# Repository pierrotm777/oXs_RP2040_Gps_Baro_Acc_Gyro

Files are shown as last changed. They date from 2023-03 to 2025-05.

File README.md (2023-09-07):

# oXs_RP2040_Gps_Baro_Acc_Gyro
 Multi Telemetry Protocols RP2040 Full version
 
## PCBWAY board link
You can find my shared pcb project [here](https://www.pcbway.com/project/shareproject/oXs_RP2040_Full_fdfb35e8.html).

 <object data="http://yoursite.com/the.pdf" type="application/pdf" width="700px" height="700px">
    <embed src="http://yoursite.com/the.pdf">
        <p>This browser does not support PDFs. Please download the PDF to view it: <a href="http://yoursite.com/the.pdf">Download PDF</a>.</p>
    </embed>
</object>

xfun::embed_file("homework.pdf")

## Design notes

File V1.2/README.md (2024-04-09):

# oXs RP2040 Transmitter (version Full telemetry)

This version use my last oXs RP2040 Telemetry board (V1.2).  

## Schematic
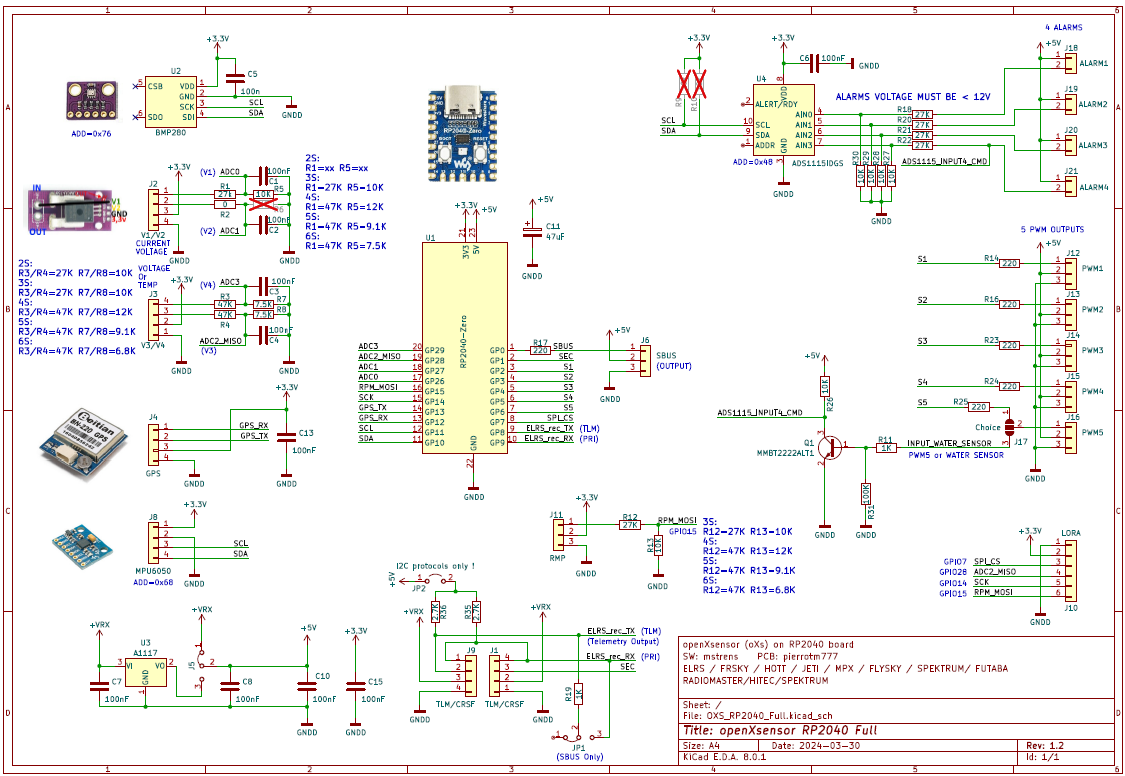
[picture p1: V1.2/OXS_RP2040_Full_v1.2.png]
Schematic
  

## Print Circuit Board
  <table border="2">
  <tr>
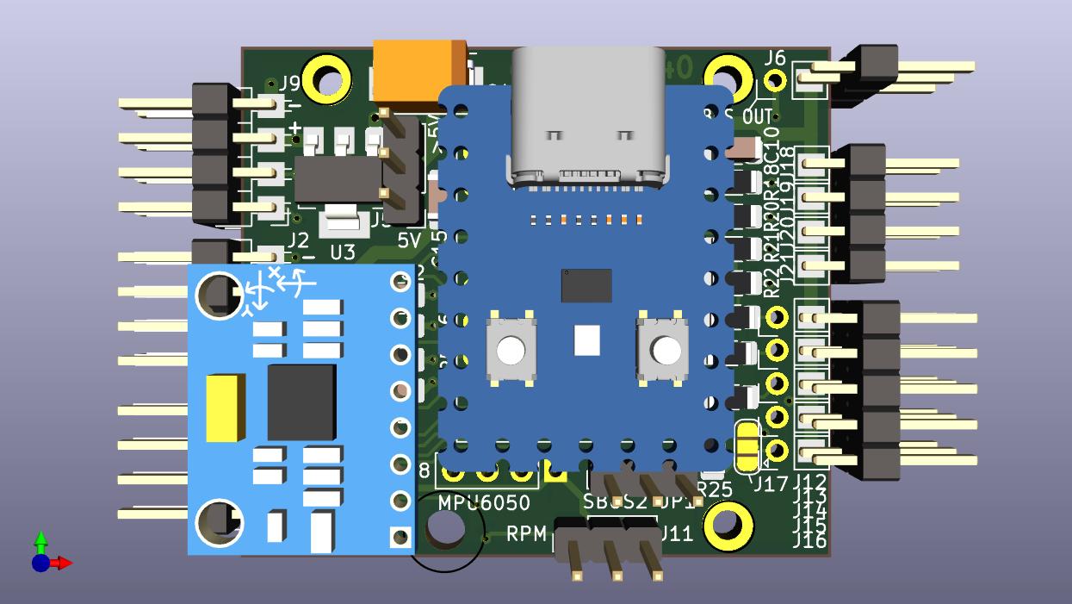
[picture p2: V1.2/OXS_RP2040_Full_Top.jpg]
  <td></td>
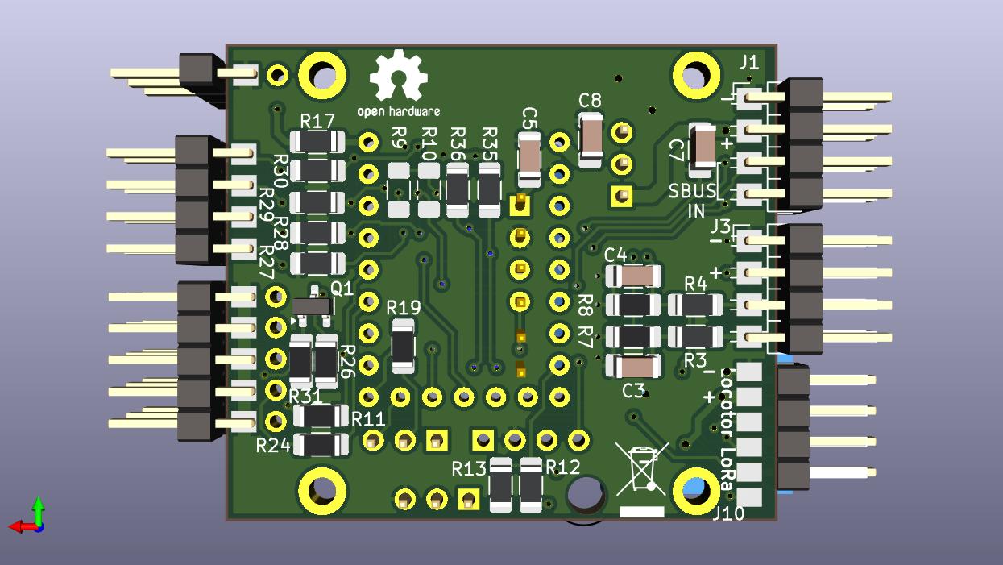
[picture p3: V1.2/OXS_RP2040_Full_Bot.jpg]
  <td></td>
  </tr>
  </table>

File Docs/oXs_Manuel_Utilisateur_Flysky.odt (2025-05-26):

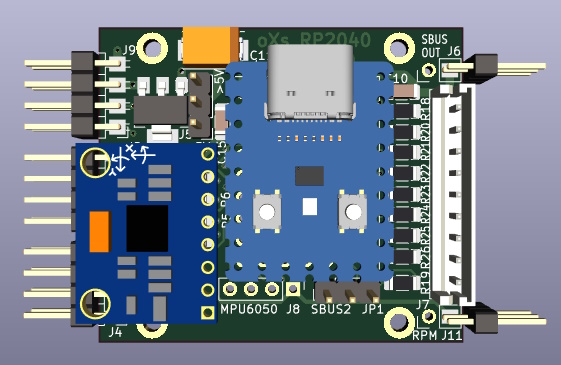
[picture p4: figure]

oXs RP2040

Nouvelle version

openXsensor

pour un RP2040-Zero

Manuel Utilisateur FlySky

# 1 Alimentation

## 1.1 Alimentation du module

Le circuit imprimé est équipé d’un régulateur de tension 5v.

Il peut être mis en ou hors fonction selon l’accu de réception utilisé.

Accus inférieur ou égal à 5V :

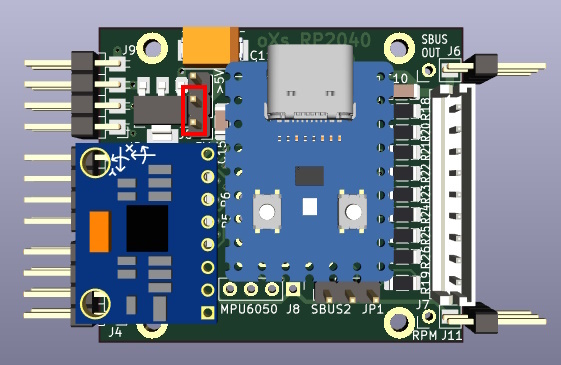
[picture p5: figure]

Accus supérieur à 5V :

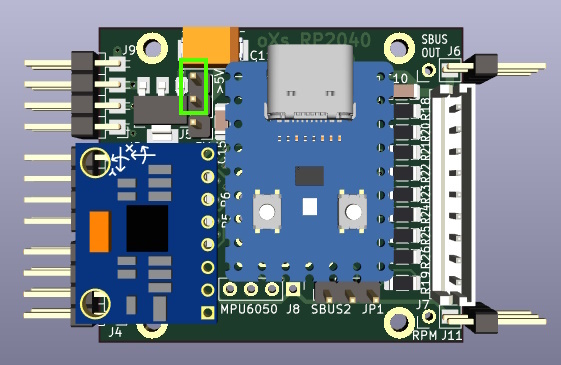
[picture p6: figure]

## 1.2 Limite du RP2040

Le RP2040 ne supporte pas de tension supérieure à 3,3v en entrée !!!!

Toute tension supérieure détruira le composant !!!!

# 2 FlySky IBUS

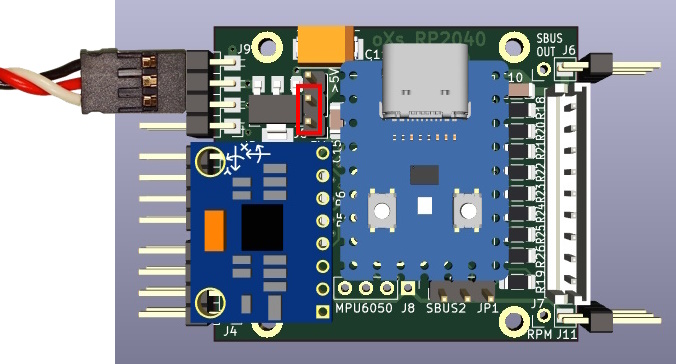
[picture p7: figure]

PROTOCOL=I TLM=8

3 Les capteurs

3.1 Le GPS

Différents récepteurs GPS sont utilisables :

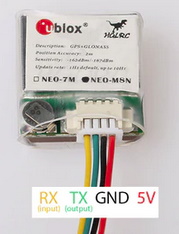
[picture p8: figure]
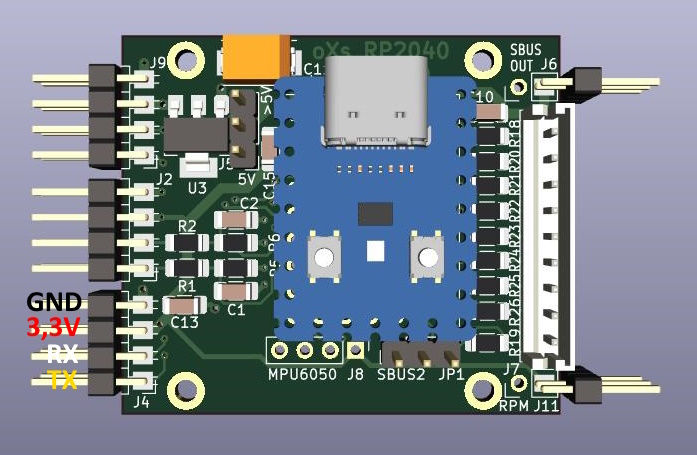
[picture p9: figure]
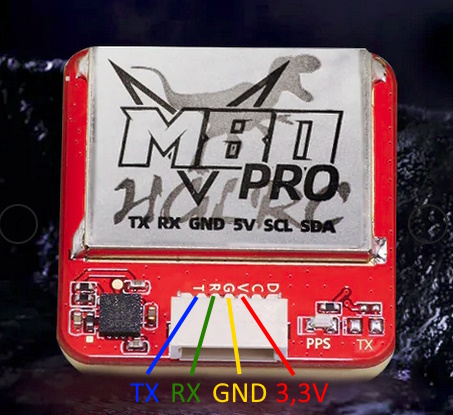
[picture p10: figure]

## 3.2 Le baromètre

Le capteur BMP280 est déjà soudé sous le RP2040.

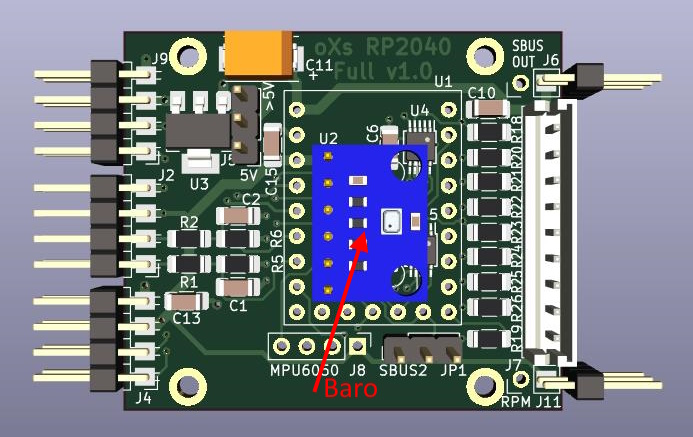
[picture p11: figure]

## 3.3 Sonde Pitot (capteur de pression différentielle)

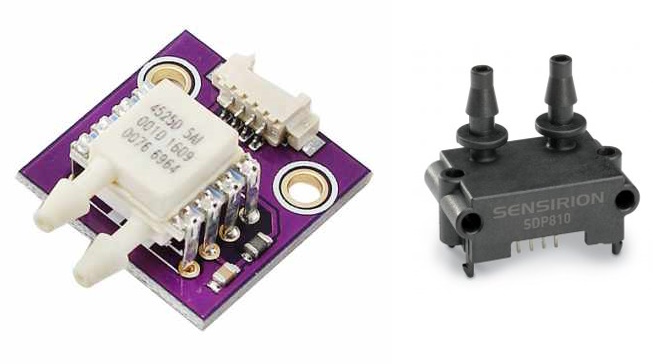
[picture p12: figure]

La sonde Pitot permet de connaître la vitesse horizontale du modèle.

Il permet aussi de calculer la vitesse verticale compensée.

Différents capteurs sont utilisables :

* MS4525D0_A ou SDP3X (x=1,2,3) ou SDP8xx .

Ces capteurs sont chers, les versions SDP sont donc à privilégier.

Ces capteurs sont à câbler sur J8 avec 4 fils, 3,3v, GND, SDA et SCL.

## 3.4 Accéléromètre gyroscope

Ce capteur deux en un permet d’améliorer le temps de réaction du vario ainsi que d’obtenir les données de tangage et roulis.

On peut utiliser un MPU6050 .

Ce capteur est à câbler sur J8 avec 4 fils, 3,3v, GND, SDA et SCL.

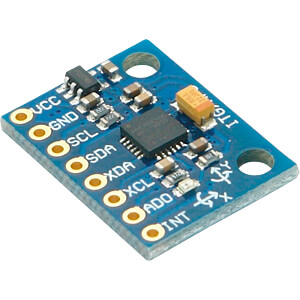
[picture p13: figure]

Après câblage de ce composant, celui-ci doit être calibré.

Pour cela, il doit être placé bien à plat.

Puis on lance la commande suivante :

MPUCAL puis ENTREE

## 3.5 Les entrées analogiques du RP2040

Le RP2040 Zero possède seulement 4 entrées analogiques, V1 à V4.

Elles utilisent les pattes 26 à 29.

V1=26 V2=27 V3=28 V4=29

V1 est attribué au voltage d’un accu de propulsion et V2 au courant consommé.

V3 et V4 retournent deux tensions ou deux températures.

Pour lire des température il faudra définir :

TEMP=1 (V3 retournera une température et V4 une tensions.

Chacune des 4 entrées possèdent un pont de résistance qui doit être calculé en fonction de la tension à lire de sorte que le rp2040 reçoive un maximum de 3,3v pour la tension maximum à lire.

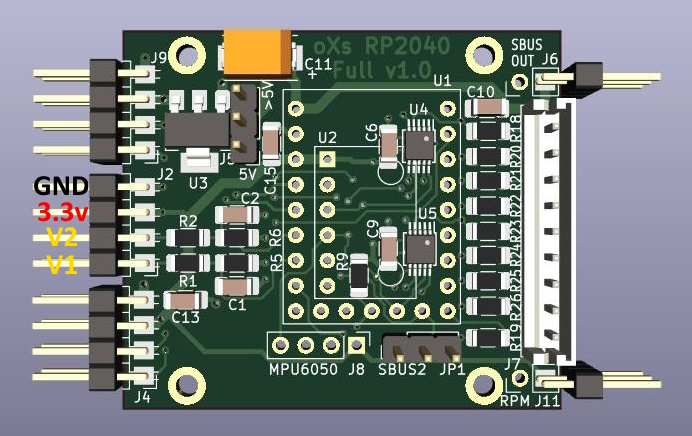
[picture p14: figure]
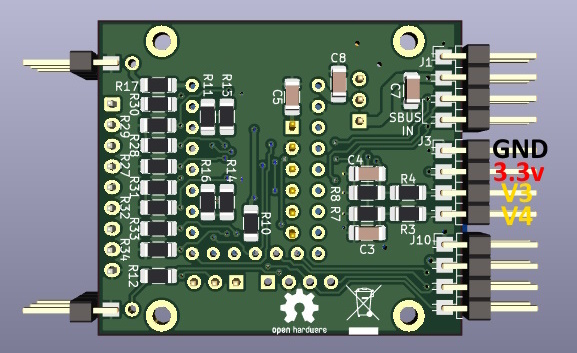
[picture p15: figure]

### 3.5.1 Tension et courant accu moteur (V1/V2)

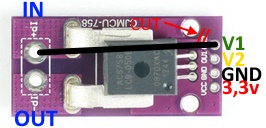
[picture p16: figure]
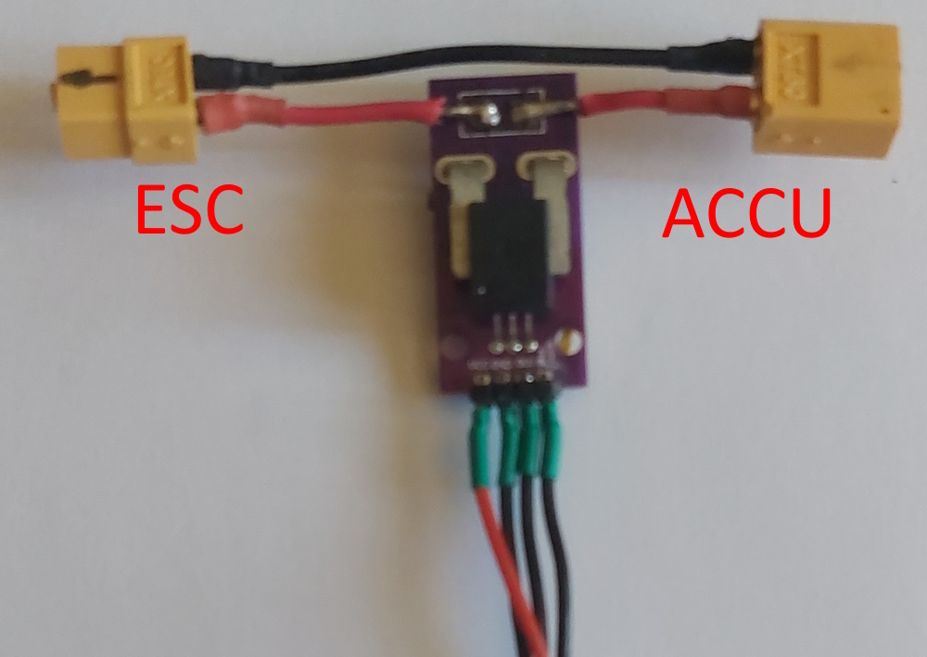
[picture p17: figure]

Pour lire le courant, on utilisera de préférence

un capteur de type ACFS758.

Il en existe différents types avec des courant maximum de 50A à 150A.

La tension de sortie pour les 50B, 100B et 150B est de 1,65 V.

Pas besoin donc de pont de résistance.

### 3.5.2 Tensions V3 et V4

Après câblage des bonnes résistances pour V3 (R4,R8) et V4(R3,R4), il est possible de lire deux tensions supplémentaires.

### 3.5.3 Capteurs de température V3 et V4

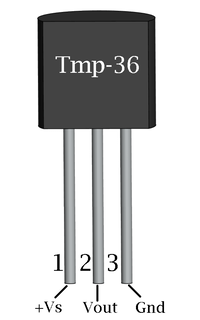
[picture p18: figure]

En fonction du besoin, on peut utiliser un ou deux capteurs de température.

On utilisera de préférence un TMP36.

Pour un seul capteur seulement on définira :

TEMP=1

La sortie de V3 sera utilisée pour ce capteur et V4 sera utilisable pour une tension.

Pour deux capteurs, on définira :

TEMP=2

Les sorties de V3 et V4 seront alors utilisées pour deux températures.

## 3.6 Capteur compte tours

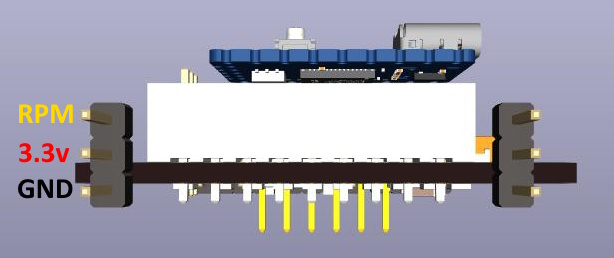
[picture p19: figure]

Ce capteur permet de connaître la vitesse de rotation d’un moteur.

Il utilise la patte 15 du RP2040.

On peut utiliser différents composants ou module.

- capteur Hall

- capteur IR

- module HobbyKing pour ESC

Pour le configurer, on définira :

RPM=15

En fonction du nombre de pales, on attribuera un multiplicateur.

Par exemple pour une hélice à deux pâles :

RPM_MULT=0.5

## 3.7 Les convertisseurs analogiques ADS1115

Les ADS1115, U4 et U5, sont des quadruples convertisseurs analogique/numériques.

Ils permettent de convertir 4 tensions en valeurs numériques.

L’idée d’origine était de palier à la limite de 4 entrées analogiques du RP2040 et de pouvoir

mesurer un accumulateur LIPO 8S maximum (connecteur blanc de droite).

Une autre idée serait d’utiliser ces ADS1115 comme huit entrées d’alarmes.

Il faudrait alors imaginer des alarmes dont le seuil serait définit entre 0 et 3,3v.

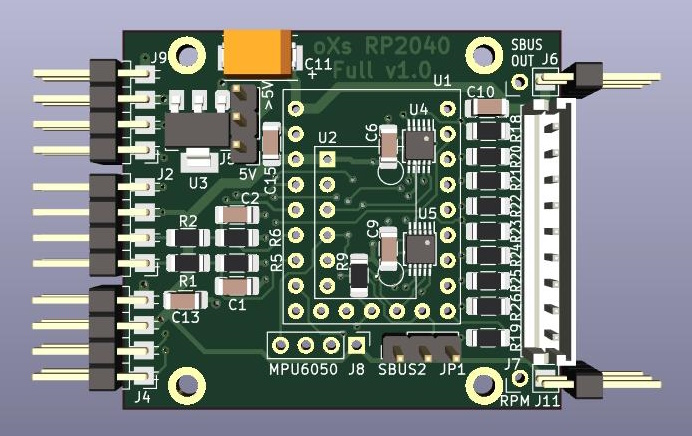
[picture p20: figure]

Pour rappel, le RP2040 ne supporte pas de tension supérieure à 3,3v en entrée !!!!

Toute tension supérieure détruira le composant !!!!

## 3.8 Sorties PWM

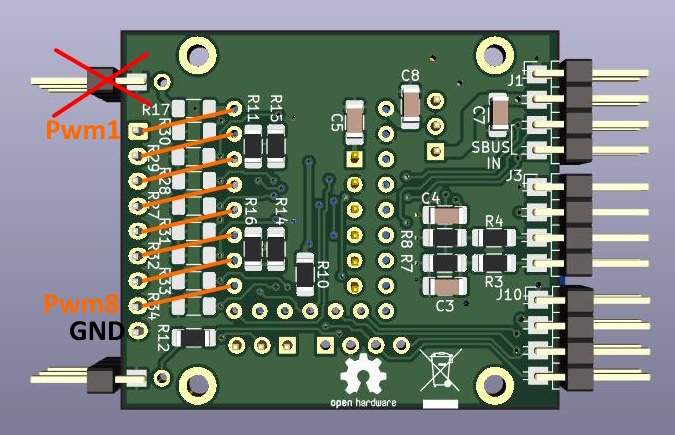
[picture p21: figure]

Si les convertisseurs analogiques ADS1115 ne sont pas utilisés, il est possible d’affecter les pattes 0 à 7 du RP2040 à 8 sorties PWM pour y connecter 8 servos.

Les résistances R18 à R34 placées entre le RP2040 et le connecteur J7 ne doivent pas être câblées.

Il faudra connecter les pattes 0 à 7 du RP2040 aux pattes 1 à 8 de J7.

Voir paragraphe 8 pour la configuration.

# 4 Configuration radio

## 4.1 Recherche des capteurs

- Brancher le module oXs un l’entrée de télémétrie du récepteur Frsky.

- Allumer le récepteur.

- Créer un nouveau modèle avec le protocole Frsky D16 ou D16 EU.

- Réaliser l’appairage du récepteur à l’émetteur (BIND).

- Aller dans l’écran de télémétrie du modèle et lancer une recherche des capteurs.

En fonction des capteurs connectés au module oXs, plusieurs lignes devraient apparaître en plus de la tension accu réception, Rssi etc.

Le GPS ne recevra pas bien s’il est utilisé en intérieur. Il met minimum 1mn pour commencer à recevoir.

Après la découverte d’au moins 4 satellites, les cordonnées ainsi que la date et l’heure, l’altitude, la vitesse horizontale et plus devraient apparaître.

Le baromètre doit retourner l’altitude par rapport au sol ainsi que la vitesse verticale.

Que l’on soit au niveau de la mer ou à 1000m d’altitude, il donnera zéro au démarrage.

C’est donc une altitude relative, pas absolue.

- Stopper la recherche des capteurs.

- Configurer Vario avec Alt .

## 4.1 Utilisation des valeurs de télémétrie dans les écrans

Les radios Frsky ou compatibles qui supportent les firmwares OpenTx ou EdgeTx disposent de pages d’écrans définissables avec ce que l’on souhaite visualiser facilement et rapidement.

On pourra facilement visualiser toutes les valeurs de télémétrie dans ces écrans.

Il est aussi possible de définir des alarmes en fonctions des valeurs de télémétrie reçues.

Page 0 Manuel utilisateur oXs RP2040 v1.0

Page 8 Manuel utilisateur oXs RP2040 v1.0

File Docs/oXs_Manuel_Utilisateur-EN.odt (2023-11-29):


oXs RP2040

New version

openXsensor

for RP2040-Zero

User Manual oXs RP2040

# THIS DOCUMENT

## Versions

Version du Manuel | Date | Raison de l’évolution
1.0 | 12/05/2023 | Création

## Thanks

This project is based on the work of Michel Strens who created the code.

Thanks to him for this wonderful work as well as his listening.

The code can be downloaded from:

https://github.com/mstrens/oXs_on_RP2040.

## Warning

I am in no way responsible for any damage that may result from the misuse or possible malfunction of the oXs RP2040 module, and/or the associated software.

It is therefore up to the end user to measure it, to assume the risks and to respect the legislation in force according to the country of use.

## Content

This document describes the creation of an oXs RP2040 telemetry module as well as its configuration.

## Supported protocols

oXs RP2040 is MULTI protocols.

It supports the following RC telemetry protocols:

ExpressLRS(CRSF)

FRSKY (S-Port or FBUS)

Graupner (HOTT)

Multiplex (M-LINK)

FLYSKY (IBUS)

Futaba ((SBUS2)

Spektrum (SRXL2)

Jeti Ex, Jeti ExBus

This project can be interfaced with 1 or 2 receivers depending on the protocol.

## Fonctions of the oXs RP2040 module

Ce projet est prévu pour générer :

- telemetry data (e.g. when a flight controller is not used)
- PWM and/or
- Sbus signals

For telemetry, it can provide
- up to 4 analog voltages measurement (with scaling and offset) (optional)
- one RPM measurement; a scaling (SCALE4) can be used to take care e.g. of number of blades (optional)
- the altitude and the vertical speed when connected to a pressure sensor (optional)
- the airspeed when connected to a differential pressure sensor (and a pitot tube) (optional)
- compensated vertical speed when connected to a baro + a differentil pressure sensor
- Pitch and Roll when conncted to a MP6050 sensor (optional);
- GPS data (longitude, latitude, speed, altitude,...) (optional)
Note: vertical speed is improved when baro sensor is combined with MP6050 sensor.
t can also provide up to 16 PWM RC channels from a CRSF/ELRS or from 1 or 2 Sbus signal (e.g Frsky or Jeti).

It can also provide SBUS signal (e.g. from 1 or 2 ELRS receivers).
When connected to 2 receivers, the generated PWM and Sbus signals will be issued from the last received Rc channels.
So this provide a kind of redundancy/diversity.

# Présentation d’oXs RP2040

## Vue d’ensemble

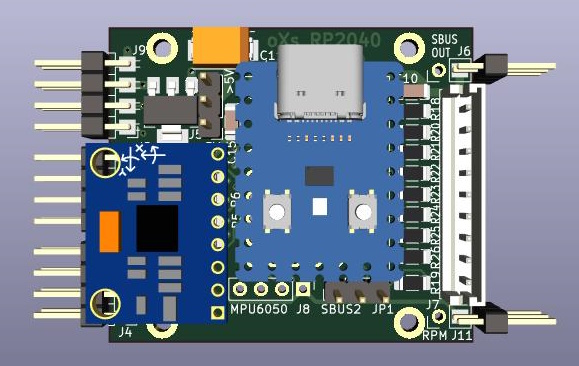
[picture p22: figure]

TX

RX

ELRS / FRSKY (sport + Fbus) / HOTT / JETI Ex/ MPX / FLYSKY / Futaba (SBUS2) / Spektrum (SRXL2)

## Spécifications du module oXs RP2040

Spécification | Valeur / Caractéristique | Note
Alimentation oXs | +5V à +12V | Mettre le cavalier « tension récepteur » sur «5v» ou «>5v» selon la valeur de la tension fournie par le récepteur
Protocoles possibles | ELRS / FRSKY (sport + Fbus) / HOTT / JETI Ex/ MPX / FLYSKY / Futaba (SBUS2) / Spektrum (SRXL2)
Port série USB | | Pour configuration avancée à l’aide d’une application type « Terminal série »
Dimensions | 45mm x 38mm | 4 perçages de 2,2mm

# Schéma du module oXs RP2040 Full

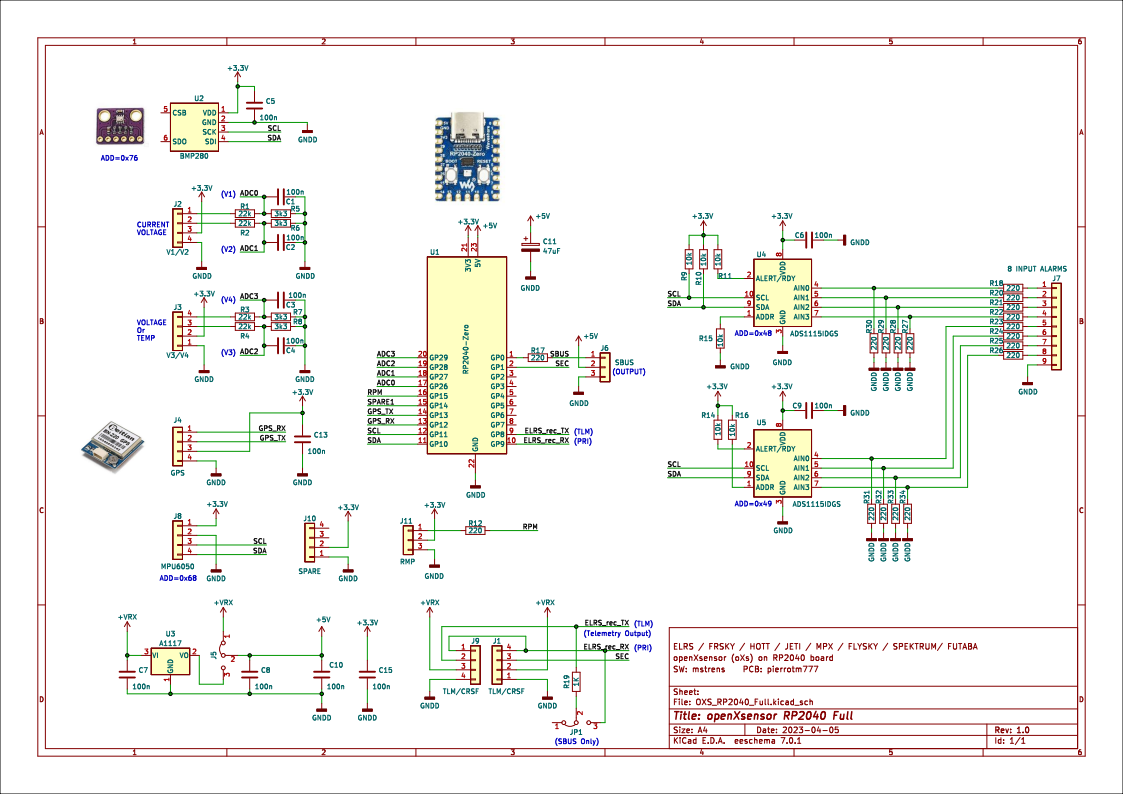
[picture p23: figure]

# Réalisation du module oXs RP2040 Full

## Circuit imprimé

La conception du circuit imprimé du décodeur oXs RP2040 a été réalisée sous KiCad.

Le dossier de fabrication (https://github.com/pierrotm777/oXs_RP2040_Gps_Baro_Acc_Gyro) est disponible sur GitHub.

## 4.2 Carte WaveShare RP2040-Zero

Le module de télémétrie utilise un Rasperri Pico de type RP2040-Zero.

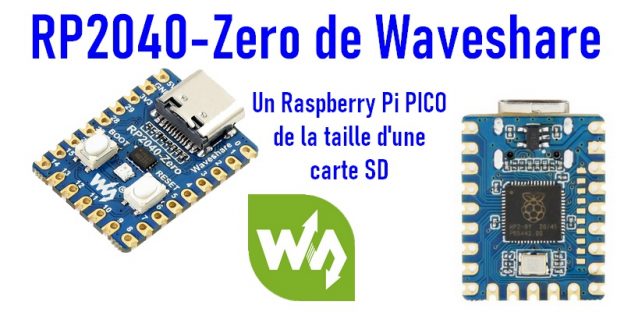
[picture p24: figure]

## 4.3 Téléchargement du Firmware dans le RP2040

Le chargement du Firmware (micro-logiciel embarqué) consiste à copier le contenu d’un fichier uf2 dans la mémoire du micro-contrôleur.

Le fichier oXs.uf2 est à télécharger sur le dépôt GitHub (https://github.com/mstrens/oXs_on_RP2040/tree/test).

## 4.4 Chargement du firmware dans le RP2040

Le RP2040 doit être connecter à votre PC via son connecteur USB tout en maintenant le bouton BOOT.

Une fenêtre doit s’ouvrir. Il suffit de copier le fichier oXs.uf2 pour charger le firmware dans le RP2040.

# 5 Configuration

## 5.1 Connexion au PC

La configuration du module se fait au travers d’un terminal .

Sur Windows, j’utilise Termite (https://www.compuphase.com/software/termite-3.4.exe) de Compuphase ou TeraTerm (https://osdn.net/projects/ttssh2/downloads/74780/teraterm-4.106.exe/) . Other treminals are possible as PuTTY or KiTTY.

A la connexion du RP2040, vous devriez voir apparaître un port COM qui faudra sélectionner.

## 5.2 Configuration du terminal

### 5.2.1 Termite


- Configurez le terminal, puis sélectionnez le port COM (ici le pour COM5).

- La vitesse peut être réglée de 9600 à 115200 sans problème, le code reconnaissant automatiquement la vitesse du terminal.

- Le contrôle de flux doit être définit (DTR/DSR)

### 5.2.2 Tera Term


## 5.3 Configuration

### 5.3.1 Visualiser la configuration du module

Utiliser la touche ENTREE .

Le module doit retourner le résultat suivant :

processing cmd

Cmd to execute:

Version = 2.2.12

Function Pin Change entering XXX=yyy (yyy=255 to disable)

Primary channels input = 255 (PRI = 5, 9, 21, 25)

Secondary channels input = 255 (SEC = 1, 13, 17, 29)

Telemetry . . . . . . . . = 255 (TLM = 0, 1, 2, ..., 29)

GPS Rx . . . . . . . . . = 255 (GPS_RX = 0, 1, 2, ..., 29)

GPS Tx . . . . . . . . . = 255 (GPS_TX = 0, 1, 2, ..., 29)

Sbus OUT . . . . . . . . = 255 (SBUS_OUT= 0, 1, 2, ..., 29)

RPM . . . . . . . . . . = 255 (RPM = 0, 1, 2, ..., 29)

SDA (I2C sensors) . . . . = 255 (SDA = 2, 6, 10, 14, 18, 22, 26)

SCL (I2C sensors) . . . . = 255 (SCL = 3, 7, 11, 15, 19, 23, 27)

PWM Channels 1, 2, 3 ,4 = 255 255 255 255 (C1 / C16= 0, 1, 2, ..., 15)

PWM Channels 5, 6, 7 ,8 = 255 255 255 255

PWM Channels 9,10,11,12 = 255 255 255 255

PWM Channels 13,14,15,16 = 255 255 255 255

Voltage 1, 2, 3, 4 = 255 255 255 255 (V1 / V4 = 26, 27, 28, 29)

Protocol is Sport (Frsky)

CRSF baudrate = 420000

Voltage parameters:

Scales : 1.000000 , 1.000000 , 1.000000 , 1.000000

Offsets: 0.000000 , 0.000000 , 0.000000 , 0.000000

No temperature sensors are connected on V3 and V4

RPM multiplier = 1.000000

Baro sensor is not detected

Acc/Gyro is not detected

Airspeed sensor is not detected

No Vspeed compensation channel defined; oXs uses default settings

First analog to digital sensor is not detected

Second analog to digital sensor is not detected

Foreseen GPS type is Ublox (configured by oXs) :GPS is not (yet) detected

Failsafe type is HOLD

Config parameters are OK

Press ? + Enter to get help about the commands

>>

### 5.3.2 Détails de la configuration

PRI Entrée FBUS SBUS ou EXBUS ou SRXL2

SEC Deuxième Entrée FBUS SBUS ou EXBUS ou SRXL2

TLM Sortie Télémétrie S-PORT JETI M-LINK HOTT

GPS_RX Connexion RX du GPS

GPS_TX Connexion TX du GPS

SBUS_OUT Sortie SBUS (résultat du meilleur signal entre PRI et SEC)

RPM Entrée tachymètre

C1 à C16 Sortie PWM (servos)

V1 à V4 Entrés analogiques (V1 dédié à la tension d’un accus, V2 au courant consommé, V3 et V4 à deux tensions supplémentaires ou deux températures)

Voici la configuration possible fonction du circuit imprimé réalisé :

Version = 2.2.12

Function Pin Change entering XXX=yyy (yyy=255 to disable)

Primary channels input = 9 (PRI = 5, 9, 21, 25)

Secondary channels input = 1 (SEC = 1, 13, 17, 29)

Telemetry . . . . . . . . = 8 (TLM = 0, 1, 2, ..., 29)

GPS Rx . . . . . . . . . = 13 (GPS_RX = 0, 1, 2, ..., 29)

GPS Tx . . . . . . . . . = 12 (GPS_TX = 0, 1, 2, ..., 29)

Sbus OUT . . . . . . . . = 0 (SBUS_OUT= 0, 1, 2, ..., 29)

RPM . . . . . . . . . . = 15 (RPM = 0, 1, 2, ..., 29)

SDA (I2C sensors) . . . . = 10 (SDA = 2, 6, 10, 14, 18, 22, 26)

SCL (I2C sensors) . . . . = 11 (SCL = 3, 7, 11, 15, 19, 23, 27)

PWM Channels 1, 2, 3 ,4 = 2 3 4 5 (C1 / C16= 0, 1, 2, ..., 15)

PWM Channels 5, 6, 7 ,8 = 255 255 255 255

PWM Channels 9,10,11,12 = 255 255 255 255

PWM Channels 13,14,15,16 = 255 255 255 255

Voltage 1, 2, 3, 4 = 255 255 255 255 (V1 / V4 = 26, 27, 28, 29)

Dans ce premier tableau, on affecte une fonction à une patte du RP2040.

L’affectation des pattes ne doit bien sûr pas être modifiée car il y aurait incompatibilité avec le circuit imprimé.

Les pattes ayant la valeur 255 ne sont pas définies.

PRI sera toujours égal à la patte 9 (mais il peut être aussi égal à 5, 9, 21 ou 25).

SEC sera toujours égal à la patte 1 ( mais il peut aussi être égal à 1, 13, 17 ou 29).

etc...

Mais, en fonction du protocole choisi et des fonctions utilisées, certaines pattes resteront à 255 donc non définies.

Pour définir une patte, il suffit de taper dans le terminal TLM=8 par exemple ou TLM=255 pour la désaffecter.

Pour connaître toutes les commandes disponibles, il suffit de taper ? puis ENTREE.

Commands can be entered to change the config parameters

- To activate a function, select the pin and enter function code = pin number (e.g. PRI=1)

Function Code Valid pins number

Primary channels input PRI = 5, 9, 21, 25

Secondary channels input SEC = 1, 13, 17, 29

Telemetry TLM = 0, 1, 2, ..., 29

GPS Rx GPS_RX = 0, 1, 2, ..., 29

GPS Tx GPS_TX = 0, 1, 2, ..., 29

Sbus OUT SBUS_OUT= 0, 1, 2, ..., 29

RPM (only for Sport) RPM = 0, 1, 2, ..., 29

SDA (baro sensor) SDA = 2, 6, 10, 14, 18, 22, 26

SCL (baro sensor) SCL = 3, 7, 11, 15, 19, 23, 27

PWM Channels 1, ..., 16 C1 / C16= 0, 1, 2, ..., 15

Voltage 1, ..., 4 V1 / V4 = 26, 27, 28, 29

- To disable a function, set pin number to 255

-To debug on USB/serial the telemetry frames, enter DEBUGTLM=Y or DEBUGTLM=N (default)

-To change the protocol, enter PROTOCOL=x where x= S(Sport Frsky), F(Fbus Frsky), C(CRSF/ELRS), H(Hott), M(Mpx), 2(Sbus2 Futaba), J(Jeti), E(jeti Exbus), X (spektrum SRXL2) ,or I(IBus/Flysky)

-To change the CRSF baudrate, enter e.g. BAUD=420000

-To change voltage scales, enter SCALEx=nnn.ddd e.g. SCALE1=2.3 or SCALE3=0.123

Enter SCALEx=0 to avoid sending voltage x to the Transmitter (for Frsky or Jeti)

-If a TMP36 is used on V3, enter TEMP=1 (if a second one is on V4, enter TEMP=2)-To change voltage offset, enter OFFSETx=nnn.ddd e.g. OFFSET1=0.6789

-To change GPS type: for an Ublox, enter GPS=U (configured by oXs) or E (configured Externally) and for a CADIS, enter GPS=C

-To change RPM multiplicator, enter e.g. RPM_MULT=0.5 to divide RPM by 2

-To force a calibration of MP6050, enter MPUCAL

-To use a channel to setup Airspeed compensation factor and/or to select between the 2 Vspeed, enter the channel with ACC=1...16-To select the failsafe mode to HOLD, enter FAILSAFE=H

-To set the failsafe values on the current position, enter SETFAILSAFE

-To get the internal telemetry values currently calculated by oXs, enter FV (meaning Field Values)

-To test a protocol, you can force the internal telemetry values to some dummy values for dummy positive values, enter FVP; for dummy negative values, enter FVN

-To get the current PWM values (in micro sec, enter PWM)-To get the current config, just press Enter

Note: some changes require a reset to be applied (e.g. to unlock I2C bus)

En cas d’erreur de configuration le module en fait la remarque, par example :

Error in parameters: a pin is defined for Sbus Out but not for Primary nor Secondary channels input (PRI or SEC)

Attention: error in config parameters

### 5.3.3 Définition du protocole de télémétrie

Selon le protocole, les broches utilisées pour les canaux RC PRIMAIRES/SECONDAIRES et pour la télémétrie (TLM) varient

Protocole | PRI | SEC | TLM | Commentaire
C(ELRS) | (TX de Rx1) | (TX de Rx2) | (RX de RX1)
S(Frsky sport) | (Sbus de Rx1) | (Sbus de Rx2) | (Sport de RX1 ou Rx2) | (1)
F(Frsky Fbus) | Fbus de Rx1 | (Sbus de Rx2) | Non utilisé | (2)
J(Jeti ex) | (Sbus de Rx1) | (Sbus de Rx2) | (Ex de Rx1 ou Rx2)
E(Jeti Exbus) | Exbus de Rx1 | (Sbus de Rx2) | Non utilisé | (2)
H(Hott) | (Sbus de Rx1) | (Sbus de Rx2) | (tlm de RX1 ou Rx2) | (1)
M(Multiplex) | (Sbus de Rx1) | (Sbus de Rx2) | (tlm de RX1 ou Rx2) | (1)
I(Flysky Ibus) | (Sbus de Rx1) | (Sbus de Rx2) | (Ibus de RX1 ou Rx2) | (1)
L(Spektrum Srxl2) | Srxl de Rx1 | Non utilisé | Non utilisé | (2)
2(Futaba Sbus2) | Sbus2 de Rx1 | (Sbus de Rx2) | Sbus2 de Rx1 via 1Kohm | (3)

# Remarque : les broches entre () signifient qu'elles sont facultatives.

(1) pour la sécurité, insérez une résistance de 1 kOhm entre la broche TLM et Rx

(2) pour la sécurité, insérez une résistance de 1 kOhm entre la broche PRI et Rx

(3) Pour Futaba, la broche TLM doit être égale à la broche PRI - 1 et insérer une résistance de 1 kOhm entre PRI et TLM

Pour plus de détails, lire le fichier Readme.md (https://github.com/mstrens/oXs_on_RP2040/blob/main/README.md) .

# 6 Câblage

## 6.1 Alimentation du module

Le circuit imprimé est équipé d’un régulateur de tension 5v.

Il peut être mis en ou hors fonction selon l’accu de réception utilisé.

Accus inférieur ou égal à 5V :


Accus supérieur à 5V :


## 6.2 Limite du RP2040

Le RP2040 ne supporte pas de tension supérieure à 3,3v en entrée !!!!

Toute tension supérieure détruira le composant !!!!

# 7 Les protocoles

## 7.1 S-Port, Hott, M-Link, Ibus, Jeti Ex


S-Port PROTOCOL=S

Hott PROTOCOL=H

M-link PROTOCOL=M

Ibus PROTOCOL=I

Jeti Ex PROTOCOL=J

PRI=255 SEC=255 TLM=8

## 7.2 Sbus2, Srxl2, Jeti ExBus, Fbus


Sbus2 PROTOCOL=2

Fbus PROTOCOL=F

Srxl2 PROTOCOL=L

Jeti Exbus PROTOCOL=E

PRI=9 SEC=255 TLM=255

## 7.2 ExpressLRS (CRSF)


PROTOCOL C PRI=9 TLM=8 SBUS_OUT=0

ELRS permet de commander des servos via la sortie SbuS ou via les sorties PWM C1 à C16.

C1=1 C2=2 C3=3 C4=4 etc.

# 8 Utilisation de deux récepteurs

Tous les récepteurs ayant une sortie SBUS sont utilisables indépendamment du type de télémétrie.

On utilise les entrées PRI=9, SEC=1 et SBUS_OUT=0.

Le module version Full n’a pas de sortie PWM directement accessibles sur le circuit imprimé,

mais il est possible de souder des connecteurs sur les pattes 0 à 7 du RP2040.

Il faut alors affecter ces 8 sorties PWM au RP2040.

C1=0 à C8=7.

On peut très bien affecter ces sorties selon nos besoins sachant que le RP2040 supporte un maximum de 16 voies.

Par exemple C9=0 à C16=7.

Les signaux PWM et Sbus générés seront émis à partir des derniers canaux Rc reçus.

Cela fournit donc une sorte de redondance/diversité.

# 9 Les capteurs

Les capteurs utilisent différentes connexions au RP2040.

- Le GPS utilise une liaison série.

- Les 4 tensions V1 à V4 utilisent une 4 entrées analogiques.

- Le tachymètre utilise une entrée numérique.

- Tous les autres capteurs utilisent une connexion I2C.

* capteur de pression (carte GY63 ou GY86 basée sur MS5611, SPL06 ou BMP280) pour obtenir l'altitude et la vitesse verticale

* un capteur de pression différentielle MS4525D0_A ou SDP3X (x=1,2,3) ou SDP8xx pour obtenir la vitesse (et la vitesse verticale compensée)

* un MP6050 (acc+gyroscope ex GY86) pour améliorer le temps de réaction du vario ou pour obtenir du tangage/roulis

* 1 ou 2 ADS1115 si vous souhaitez mesurer plus de 4 tensions analogiques

## 9.1 Le GPS

Différents récepteurs GPS sont utilisables :


## 9.2 Sonde Pitot (capteur de pression différentielle)

La sonde Pitot permet de connaître la vitesse horizontale du modèle.

Il permet aussi de calculer la vitesse verticale compensée.

Différents capteurs sont utilisables :

* MS4525D0_A ou SDP3X (x=1,2,3) ou SDP8xx .

Ces capteurs sont chers, les versions SDP sont donc à privilégier.

Ces capteurs sont à câbler sur J8 avec 4 fils, 3,3v, GND, SDA et SCL.

## 9.3 Le baromètre

Le capteur BMP280 est soudé sous le RP2040.


## 9.4 Accéléromètre gyroscope

Ce capteur deux en un permet d’améliorer le temps de réaction du vario ainsi que d’obtenir les données de tangage et roulis.

On peut utiliser un MPU6050 .

Ce capteur est à câbler sur J8 avec 4 fils, 3,3v, GND, SDA et SCL.


Après câblage de ce composant, celui-ci doit être calibré.

Pour cela, il doit être placé bien à plat.

Puis on lance la commande suivante :

MPUCAL puis ENTREE

## 9.5 Les entrées analogiques du RP2040

Le RP2040 Zero possède seulement 4 entrées analogiques, V1 à V4.

Elles utilisent les pattes 26 à 29.

V1=26 V2=27 V3=28 V4=29

V1 est attribué au voltage d’un accu de propulsion et V2 au courant consommé.

V3 et V4 retournent deux tensions ou deux températures.

Pour lire des température il faudra définir :

TEMP=1 (V3 retournera une température et V4 une tensions.

TEMP=2 (V3 et V4 retourneront des températures).

Chacune des 4 entrées possèdent un pont de résistance qui doit être calculé en fonction de la tension à lire de sorte que le rp2040 reçoive un maximum de 3,3v pour la tension maximum à lire.


### 9.5.1 Tension accu moteur (V1)

Calcule du pont de résistance afin d’obtenir une tension de 3,3v pour la tension maximum.


### Pour par exemple une de 21v (4 x 4,2v soir 5S) :

R1 = 4700 Ohms (voir R1 sur le schéma)

R2 = 1000 Ohms (voir R5 sur le schéma)

Vout = 3,33v

### Par défaut, la configuration des tensions est définie ainsi :

Voltage parameters:

Scales : 1.000000 , 1.000000 , 1.000000 , 1.000000

Offsets: 0.000000 , 0.000000 , 0.000000 , 0.000000

Après câblage des bonnes résistances, on utilise un multimètre connecté entre la patte 26 du RP2040 et GND, on lit la tension sur la radio et sur le multimètre.

On va en déduire une compensation à ajouter à la configuration du RP2040.

Dans mon cas, j’ai dû définir V1 ainsi :

Voltage parameters:

Scales : 6.330000 , 50.000000 , 1.000000 , 1.000000

Offsets: 0.000000 , 82500.000000 , 0.000000 , 0.000000

### 9.5.2 Courant accu moteur (V2)


Pour lire le courant, on utilisera de préférence

un capteur de type ACFS758.

Il en existe différents types avec des courant maximum de 50A à 150A.

La tension de sortie pour les 50B, 100B et 150B est de 1,65 V.

Pas besoin donc de pont de résistance.

On utilisera donc :

R1 = 0 Ohm (voir R2 sur le schéma)

R2 = non câblé (voir R6 sur le schéma)

Donc, tout ce que vous avez à faire est de définir :

Après câblage de R2 on modifiera la configuration du RP2040 selon le modèle du ACS758.

Modèle | Scale | Offset
ACS758-50B | 25 | 41250
ACS758-100B | 50 | 82500
ACS758-150B | 75,188 | 124060,15

Dans mon cas, pour un ACS758-100B j’ai dû définir V2 ainsi :

Voltage parameters:

Scales : 6.330000 , 50.000000 , 1.000000 , 1.000000

Offsets: 0.000000 , 82500.000000 , 0.000000 , 0.000000

### 9.5.3 Tensions V3 et V4

Après câblage des bonnes résistances pour V3 (R4,R8) et V4(R3,R4), on utilise un multimètre connecté entre les pattes 28 ou 29 du RP2040 et GND, on lit la tension sur la radio et sur le multimètre.

On va en déduire une compensation à ajouter à la configuration du RP2040.

A vous de définir Scale et Offset selon vos besoins/

Voltage parameters:

Scales : 6.330000 , 50.000000 , 1.000000 , 1.000000

Offsets: 0.000000 , 82500.000000 , 0.000000 , 0.000000

### 9.5.4 Capteurs de température


En fonction du besoin, on peut utiliser un ou deux capteurs de température.

On utilisera de préférence un TMP36.

Pour un seul capteur seulement on définira :

TEMP=1

La sortie de V3 sera utilisée pour ce capteur et V4 sera utilisable pour une tension.

Pour deux capteurs, on définira :

TEMP=2

Les sorties de V3 et V4 seront alors utilisées pour deux températures.

## 9.6 Capteur compte tours


Ce capteur permet de connaître la vitesse de rotation d’un moteur.

Il utilise la patte 15 du RP2040.

On peut utiliser différents composants ou module.

- capteur Hall (ajouter une résistance entre GPIO15 et GND afin d’obtenir 3,3v maxi sur GPIO15)

- capteur IR (ajouter une résistance entre GPIO15 et GND afin d’obtenir 3,3v maxi sur GPIO15)

- module HobbyKing pour ESC

Pour le configurer, on définira :

RPM=15

En fonction du nombre de pales, on attribuera un multiplicateur.

Par exemple pour une hélice à deux pâles :

RPM_MULT=0.5

## 9.7 Les convertisseurs analogiques ADS1115

Les ADS1115, U4 et U5, sont des quadruples convertisseurs analogique/numériques.

Ils permettent de convertir 4 tensions en valeurs numériques.

L’idée d’origine était de palier à la limite de 4 entrées analogiques du RP2040 et de pouvoir

mesurer un accumulateur LIPO 8S maximum (connecteur blanc de droite).

Une autre idée serait d’utiliser ces ADS1115 comme huit entrées d’alarmes.

Il faudrait alors imaginer des alarmes dont le seuil serait définit entre 0 et 3,3v.


Pour rappel, le RP2040 ne supporte pas de tension supérieure à 3,3v en entrée !!!!

Toute tension supérieure détruira le composant !!!!

## 9.8 Sorties PWM


Si les convertisseurs analogiques ADS1115 ne sont pas utilisés, il est possible d’affecter les pattes 0 à 7 du RP2040 à 8 sorties PWM pour y connecter 8 servos.

Les résistances R18 à R34 placées entre le RP2040 et le connecteur J7 ne doivent pas être câblées.

Il faudra connecter les pattes 0 à 7 du RP2040 aux pattes 1 à 8 de J7.

Voir paragraphe 8 pour la configuration.

# 10 Réglage du Failsafe

oXs possède une fonction de Failsafe sur les sorties PWM et SBUS.

* Pour le protocole ELRS, oXs ne reçoit aucune donnée du canal RC ou des récepteurs lorsque la connexion RF est perdue. Si oXs est connecté à 2 récepteurs (via PRI et SEC), oXs générera des signaux PWM et Sbus sur les dernières données reçues. Si oXs ne reçoit plus de données du ou des récepteurs, il continuera à générer des signaux PWM et/ou SBUS en fonction de la configuration de sécurité intégrée stockée dans oXs.

* Pour les protocoles Frsky/Jeti... où Sbus, les valeurs de sécurité sont normalement définies à l'intérieur du récepteur et le récepteur continue à générer un signal Sbus même si la connexion RF est perdue. Pourtant, lorsque la connexion est perdue, le signal Sbus contient des drapeaux indiquant que certaines données sont manquantes ou que la sécurité intégrée a été appliquée. Lorsque oXs est connecté à 2 récepteurs différents, il donne la priorité au signal Sbus PRI sauf si le signal SEC est OK et PRI n'est pas OK (pas de signal, trame manquante, failsafe). Ainsi, pour Frsky/Jeti, oXs n'a pas à s'occuper de sa propre configuration de sécurité (sauf si oXs ne recoit plus de signal Sbus - par exemple en raison d'un problème de câblage).

* Le failsafe oXs a 3 options :

* "Hold" = failsafe sera les dernières valeurs des canaux Rc connus juste avant que la connexion ne soit perdue ; pour sélectionner cette option, utilisez l'interface série avec la commande FAILSAFE=H.

* Sauvegarder comme sécurité intégrée les valeurs actuelles des canaux RC à l'aide de l'interface série avec la commande SETFAILSAFE.

* Sauvegarder en tant que sécurité intégrée les valeurs actuelles des canaux RC à l'aide du bouton "boot" du RP2040. Pour activer cette option, double-cliquez sur le bouton. La led doit devenir bleue fixe. Dans les 5 secondes suivantes, appuyez et maintenez le bouton "boot". La led deviendra blanche pendant 2 secondes confirmant que les valeurs sont enregistrées.

Pour les 2 dernières options, l’émetteur doit être allumé et générer les valeurs des canaux que vous souhaitez enregistrer dans oXs.

11 Documentations

Une documentation (https://github.com/mstrens/oXs_on_RP2040/blob/test/doc/fields%20per%20protocol.txt) très précise pour chaque protocole est disponible sur le github de Michel Strens.

On peut y trouver les différentes valeurs des ID par porotocole.

Page 20 Manuel utilisateur oXs RP2040 v1.0

Page 5 Manuel utilisateur oXs RP2040 v1.0

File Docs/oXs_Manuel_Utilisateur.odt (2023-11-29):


oXs RP2040

Nouvelle version

openXsensor

pour un RP2040-Zero

Manuel Utilisateur oXs RP2040

# CE DOCUMENT

## Versions

Version du Manuel | Date | Raison de l’évolution
1.0 | 11/04/2023 | Création

## Remerciement

Ce projet est basé sur le travail de Michel Strens qui en a réalisé le code .

Merci à lui pour ce formidable travail ainsi que son écoute.

Le code est téléchargeable à l’adresse suivante :

https://github.com/mstrens/oXs_on_RP2040.

## Avertissement

Je ne suis aucunement responsable des dommages qui pourraient découler de la mauvaise utilisation ou d’un éventuel dysfonctionnement du module oXs RP2040, et/ou du logiciel associé.

Il appartient donc à l’utilisateur final d’en mesurer, d’en assumer les risques et de respecter la législation en vigueur selon le pays d’utilisation.

## Contenu

Ce document décrit la réalisation d’un module de télémétrie oXs RP2040 ainsi que son paramétrage.

## Protocoles supportés

oXs RP2040 est MULTI protocoles.

Il supporte les protocoles de télémétrie RC suivants :

ExpressLRS(CRSF), FRSKY (S-Port ou FBUS), Graupner (HOTT), Multiplex (M-LINK), FLYSKY (IBUS) , Futaba ((SBUS2), Spektrum (SRXL2), Jeti Ex, Jeti ExBus.

Ce projet peut être interfacé avec 1 ou 2 récepteurs selon le protocole.

## Fonctions du module oXs RP2040

Ce projet est prévu pour générer :

- des données de télémétrie (par exemple, lorsqu'un contrôleur de vol n'est pas utilisé).

- sorties PWM pour des servos.

- signaux Sbus.

Pour la télémétrie, il peut fournir :

- jusqu'à 4 mesures de tensions analogiques (avec mise à l'échelle et décalage) (en option).

- une mesure RPM ; une mise à l'échelle (SCALE4) peut être utilisée pour prendre en compte par ex. le nombre de pâles (facultatif).

- l'altitude et la vitesse verticale lorsqu'il est connecté à un capteur de pression (en option)

- la vitesse anémométrique lorsqu'il est connecté à un capteur de pression différentielle (et un tube de Pitot) (facultatif).

- vitesse verticale compensée lorsqu'il est connecté à un baromètre + un capteur de pression différentielle.

- Pitch et Roll lorsqu'il est connecté à un capteur MP6050 (en option).

- Données GPS (longitude, latitude, vitesse, altitude,...) (en option) Remarque : la vitesse verticale est améliorée lorsque le capteur baro est combiné avec le capteur MP6050.

Il peut également fournir jusqu'à 16 canaux PWM RC à partir d'un CRSF/ELRS ou à partir de 1 ou 2 signaux Sbus (par exemple Frsky ou Jeti).

Il peut également fournir un signal SBUS (par exemple à partir de 1 ou 2 récepteurs ELRS).

Lorsqu'il est connecté à 2 récepteurs, les signaux PWM et Sbus générés seront émis à partir des derniers canaux Rc reçus. Cela fournit donc une sorte de redondance/diversité.

Chaque fonction (télémétrie/PWM/SBUS) peut être utilisée seule ou combinée avec les autres.

# Présentation d’oXs RP2040

## Vue d’ensemble


TX

RX

ELRS / FRSKY (sport + Fbus) / HOTT / JETI Ex/ MPX / FLYSKY / Futaba (SBUS2) / Spektrum (SRXL2)

## Spécifications du module oXs RP2040

Spécification | Valeur / Caractéristique | Note
Alimentation oXs | +5V à +12V | Mettre le cavalier « tension récepteur » sur «5v» ou «>5v» selon la valeur de la tension fournie par le récepteur
Protocoles possibles | ELRS / FRSKY (sport + Fbus) / HOTT / JETI Ex/ MPX / FLYSKY / Futaba (SBUS2) / Spektrum (SRXL2)
Port série USB | | Pour configuration avancée à l’aide d’une application type « Terminal série »
Dimensions | 45mm x 38mm | 4 perçages de 2,2mm

# Schéma du module oXs RP2040 Full


# Réalisation du module oXs RP2040 Full

## Circuit imprimé

La conception du circuit imprimé du décodeur oXs RP2040 a été réalisée sous KiCad.

Le dossier de fabrication (https://github.com/pierrotm777/oXs_RP2040_Gps_Baro_Acc_Gyro) est disponible sur GitHub.

## 4.2 Carte WaveShare RP2040-Zero

Le module de télémétrie utilise un Rasperri Pico de type RP2040-Zero.


## 4.3 Téléchargement du Firmware dans le RP2040

Le chargement du Firmware (micro-logiciel embarqué) consiste à copier le contenu d’un fichier uf2 dans la mémoire du micro-contrôleur.

Le fichier oXs.uf2 est à télécharger sur le dépôt GitHub (https://github.com/mstrens/oXs_on_RP2040/tree/test).

## 4.4 Chargement du firmware dans le RP2040

Le RP2040 doit être connecter à votre PC via son connecteur USB tout en maintenant le bouton BOOT.

Une fenêtre doit s’ouvrir. Il suffit de copier le fichier oXs.uf2 pour charger le firmware dans le RP2040.

# 5 Configuration

## 5.1 Connexion au PC

La configuration du module se fait au travers d’un terminal .

Sur Windows, j’utilise Termite (https://www.compuphase.com/software/termite-3.4.exe) de Compuphase ou TeraTerm (https://osdn.net/projects/ttssh2/downloads/74780/teraterm-4.106.exe/) . Other treminals are possible as PuTTY or KiTTY.

A la connexion du RP2040, vous devriez voir apparaître un port COM qui faudra sélectionner.

## 5.2 Configuration du terminal

### 5.2.1 Termite


- Configurez le terminal, puis sélectionnez le port COM (ici le pour COM5).

- La vitesse peut être réglée de 9600 à 115200 sans problème, le code reconnaissant automatiquement la vitesse du terminal.

- Le contrôle de flux doit être définit (DTR/DSR)

### 5.2.2 Tera Term


## 5.3 Configuration

### 5.3.1 Visualiser la configuration du module

Utiliser la touche ENTREE .

Le module doit retourner le résultat suivant :

processing cmd

Cmd to execute:

Version = 2.2.12

Function Pin Change entering XXX=yyy (yyy=255 to disable)

Primary channels input = 255 (PRI = 5, 9, 21, 25)

Secondary channels input = 255 (SEC = 1, 13, 17, 29)

Telemetry . . . . . . . . = 255 (TLM = 0, 1, 2, ..., 29)

GPS Rx . . . . . . . . . = 255 (GPS_RX = 0, 1, 2, ..., 29)

GPS Tx . . . . . . . . . = 255 (GPS_TX = 0, 1, 2, ..., 29)

Sbus OUT . . . . . . . . = 255 (SBUS_OUT= 0, 1, 2, ..., 29)

RPM . . . . . . . . . . = 255 (RPM = 0, 1, 2, ..., 29)

SDA (I2C sensors) . . . . = 255 (SDA = 2, 6, 10, 14, 18, 22, 26)

SCL (I2C sensors) . . . . = 255 (SCL = 3, 7, 11, 15, 19, 23, 27)

PWM Channels 1, 2, 3 ,4 = 255 255 255 255 (C1 / C16= 0, 1, 2, ..., 15)

PWM Channels 5, 6, 7 ,8 = 255 255 255 255

PWM Channels 9,10,11,12 = 255 255 255 255

PWM Channels 13,14,15,16 = 255 255 255 255

Voltage 1, 2, 3, 4 = 255 255 255 255 (V1 / V4 = 26, 27, 28, 29)

Protocol is Sport (Frsky)

CRSF baudrate = 420000

Voltage parameters:

Scales : 1.000000 , 1.000000 , 1.000000 , 1.000000

Offsets: 0.000000 , 0.000000 , 0.000000 , 0.000000

No temperature sensors are connected on V3 and V4

RPM multiplier = 1.000000

Baro sensor is not detected

Acc/Gyro is not detected

Airspeed sensor is not detected

No Vspeed compensation channel defined; oXs uses default settings

First analog to digital sensor is not detected

Second analog to digital sensor is not detected

Foreseen GPS type is Ublox (configured by oXs) :GPS is not (yet) detected

Failsafe type is HOLD

Config parameters are OK

Press ? + Enter to get help about the commands

>>

### 5.3.2 Détails de la configuration

PRI Entrée FBUS SBUS ou EXBUS ou SRXL2

SEC Deuxième Entrée FBUS SBUS ou EXBUS ou SRXL2

TLM Sortie Télémétrie S-PORT JETI M-LINK HOTT

GPS_RX Connexion RX du GPS

GPS_TX Connexion TX du GPS

SBUS_OUT Sortie SBUS (résultat du meilleur signal entre PRI et SEC)

RPM Entrée tachymètre

C1 à C16 Sortie PWM (servos)

V1 à V4 Entrés analogiques (V1 dédié à la tension d’un accus, V2 au courant consommé, V3 et V4 à deux tensions supplémentaires ou deux températures)

Voici la configuration possible fonction du circuit imprimé réalisé :

Version = 2.2.12

Function Pin Change entering XXX=yyy (yyy=255 to disable)

Primary channels input = 9 (PRI = 5, 9, 21, 25)

Secondary channels input = 1 (SEC = 1, 13, 17, 29)

Telemetry . . . . . . . . = 8 (TLM = 0, 1, 2, ..., 29)

GPS Rx . . . . . . . . . = 13 (GPS_RX = 0, 1, 2, ..., 29)

GPS Tx . . . . . . . . . = 12 (GPS_TX = 0, 1, 2, ..., 29)

Sbus OUT . . . . . . . . = 0 (SBUS_OUT= 0, 1, 2, ..., 29)

RPM . . . . . . . . . . = 15 (RPM = 0, 1, 2, ..., 29)

SDA (I2C sensors) . . . . = 10 (SDA = 2, 6, 10, 14, 18, 22, 26)

SCL (I2C sensors) . . . . = 11 (SCL = 3, 7, 11, 15, 19, 23, 27)

PWM Channels 1, 2, 3 ,4 = 2 3 4 5 (C1 / C16= 0, 1, 2, ..., 15)

PWM Channels 5, 6, 7 ,8 = 255 255 255 255

PWM Channels 9,10,11,12 = 255 255 255 255

PWM Channels 13,14,15,16 = 255 255 255 255

Voltage 1, 2, 3, 4 = 255 255 255 255 (V1 / V4 = 26, 27, 28, 29)

Dans ce premier tableau, on affecte une fonction à une patte du RP2040.

L’affectation des pattes ne doit bien sûr pas être modifiée car il y aurait incompatibilité avec le circuit imprimé.

Les pattes ayant la valeur 255 ne sont pas définies.

PRI sera toujours égal à la patte 9 (mais il peut être aussi égal à 5, 9, 21 ou 25).

SEC sera toujours égal à la patte 1 ( mais il peut aussi être égal à 1, 13, 17 ou 29).

etc...

Mais, en fonction du protocole choisi et des fonctions utilisées, certaines pattes resteront à 255 donc non définies.

Pour définir une patte, il suffit de taper dans le terminal TLM=8 par exemple ou TLM=255 pour la désaffecter.

Pour connaître toutes les commandes disponibles, il suffit de taper ? puis ENTREE.

Commands can be entered to change the config parameters

- To activate a function, select the pin and enter function code = pin number (e.g. PRI=1)

Function Code Valid pins number

Primary channels input PRI = 5, 9, 21, 25

Secondary channels input SEC = 1, 13, 17, 29

Telemetry TLM = 0, 1, 2, ..., 29

GPS Rx GPS_RX = 0, 1, 2, ..., 29

GPS Tx GPS_TX = 0, 1, 2, ..., 29

Sbus OUT SBUS_OUT= 0, 1, 2, ..., 29

RPM (only for Sport) RPM = 0, 1, 2, ..., 29

SDA (baro sensor) SDA = 2, 6, 10, 14, 18, 22, 26

SCL (baro sensor) SCL = 3, 7, 11, 15, 19, 23, 27

PWM Channels 1, ..., 16 C1 / C16= 0, 1, 2, ..., 15

Voltage 1, ..., 4 V1 / V4 = 26, 27, 28, 29

- To disable a function, set pin number to 255

-To debug on USB/serial the telemetry frames, enter DEBUGTLM=Y or DEBUGTLM=N (default)

-To change the protocol, enter PROTOCOL=x where x= S(Sport Frsky), F(Fbus Frsky), C(CRSF/ELRS), H(Hott), M(Mpx), 2(Sbus2 Futaba), J(Jeti), E(jeti Exbus), X (spektrum SRXL2) ,or I(IBus/Flysky)

-To change the CRSF baudrate, enter e.g. BAUD=420000

-To change voltage scales, enter SCALEx=nnn.ddd e.g. SCALE1=2.3 or SCALE3=0.123

Enter SCALEx=0 to avoid sending voltage x to the Transmitter (for Frsky or Jeti)

-If a TMP36 is used on V3, enter TEMP=1 (if a second one is on V4, enter TEMP=2)-To change voltage offset, enter OFFSETx=nnn.ddd e.g. OFFSET1=0.6789

-To change GPS type: for an Ublox, enter GPS=U (configured by oXs) or E (configured Externally) and for a CADIS, enter GPS=C

-To change RPM multiplicator, enter e.g. RPM_MULT=0.5 to divide RPM by 2

-To force a calibration of MP6050, enter MPUCAL

-To use a channel to setup Airspeed compensation factor and/or to select between the 2 Vspeed, enter the channel with ACC=1...16-To select the failsafe mode to HOLD, enter FAILSAFE=H

-To set the failsafe values on the current position, enter SETFAILSAFE

-To get the internal telemetry values currently calculated by oXs, enter FV (meaning Field Values)

-To test a protocol, you can force the internal telemetry values to some dummy values for dummy positive values, enter FVP; for dummy negative values, enter FVN

-To get the current PWM values (in micro sec, enter PWM)-To get the current config, just press Enter

Note: some changes require a reset to be applied (e.g. to unlock I2C bus)

En cas d’erreur de configuration le module en fait la remarque, par example :

Error in parameters: a pin is defined for Sbus Out but not for Primary nor Secondary channels input (PRI or SEC)

Attention: error in config parameters

### 5.3.3 Définition du protocole de télémétrie

Selon le protocole, les broches utilisées pour les canaux RC PRIMAIRES/SECONDAIRES et pour la télémétrie (TLM) varient

Protocole | PRI | SEC | TLM | Commentaire
C(ELRS) | (TX de Rx1) | (TX de Rx2) | (RX de RX1)
S(Frsky sport) | (Sbus de Rx1) | (Sbus de Rx2) | (Sport de RX1 ou Rx2) | (1)
F(Frsky Fbus) | Fbus de Rx1 | (Sbus de Rx2) | Non utilisé | (2)
J(Jeti ex) | (Sbus de Rx1) | (Sbus de Rx2) | (Ex de Rx1 ou Rx2)
E(Jeti Exbus) | Exbus de Rx1 | (Sbus de Rx2) | Non utilisé | (2)
H(Hott) | (Sbus de Rx1) | (Sbus de Rx2) | (tlm de RX1 ou Rx2) | (1)
M(Multiplex) | (Sbus de Rx1) | (Sbus de Rx2) | (tlm de RX1 ou Rx2) | (1)
I(Flysky Ibus) | (Sbus de Rx1) | (Sbus de Rx2) | (Ibus de RX1 ou Rx2) | (1)
L(Spektrum Srxl2) | Srxl de Rx1 | Non utilisé | Non utilisé | (2)
2(Futaba Sbus2) | Sbus2 de Rx1 | (Sbus de Rx2) | Sbus2 de Rx1 via 1Kohm | (3)

# Remarque : les broches entre () signifient qu'elles sont facultatives.

(1) pour la sécurité, insérez une résistance de 1 kOhm entre la broche TLM et Rx

(2) pour la sécurité, insérez une résistance de 1 kOhm entre la broche PRI et Rx

(3) Pour Futaba, la broche TLM doit être égale à la broche PRI - 1 et insérer une résistance de 1 kOhm entre PRI et TLM

Pour plus de détails, lire le fichier Readme.md (https://github.com/mstrens/oXs_on_RP2040/blob/main/README.md) .

# 6 Câblage

## 6.1 Alimentation du module

Le circuit imprimé est équipé d’un régulateur de tension 5v.

Il peut être mis en ou hors fonction selon l’accu de réception utilisé.

Accus inférieur ou égal à 5V :


Accus supérieur à 5V :


## 6.2 Limite du RP2040

Le RP2040 ne supporte pas de tension supérieure à 3,3v en entrée !!!!

Toute tension supérieure détruira le composant !!!!

# 7 Les protocoles

## 7.1 S-Port, Hott, M-Link, Ibus, Jeti Ex


S-Port PROTOCOL=S

Hott PROTOCOL=H

M-link PROTOCOL=M

Ibus PROTOCOL=I

Jeti Ex PROTOCOL=J

PRI=255 SEC=255 TLM=8

## 7.2 Sbus2, Srxl2, Jeti ExBus, Fbus


Sbus2 PROTOCOL=2

Fbus PROTOCOL=F

Srxl2 PROTOCOL=L

Jeti Exbus PROTOCOL=E

PRI=9 SEC=255 TLM=255

## 7.2 ExpressLRS (CRSF)


PROTOCOL C PRI=9 TLM=8 SBUS_OUT=0

ELRS permet de commander des servos via la sortie SbuS ou via les sorties PWM C1 à C16.

C1=1 C2=2 C3=3 C4=4 etc.

# 8 Utilisation de deux récepteurs

Tous les récepteurs ayant une sortie SBUS sont utilisables indépendamment du type de télémétrie.

On utilise les entrées PRI=9, SEC=1 et SBUS_OUT=0.

Le module version Full n’a pas de sortie PWM directement accessibles sur le circuit imprimé,

mais il est possible de souder des connecteurs sur les pattes 0 à 7 du RP2040.

Il faut alors affecter ces 8 sorties PWM au RP2040.

C1=0 à C8=7.

On peut très bien affecter ces sorties selon nos besoins sachant que le RP2040 supporte un maximum de 16 voies.

Par exemple C9=0 à C16=7.

Les signaux PWM et Sbus générés seront émis à partir des derniers canaux Rc reçus.

Cela fournit donc une sorte de redondance/diversité.

# 9 Les capteurs

Les capteurs utilisent différentes connexions au RP2040.

- Le GPS utilise une liaison série.

- Les 4 tensions V1 à V4 utilisent une 4 entrées analogiques.

- Le tachymètre utilise une entrée numérique.

- Tous les autres capteurs utilisent une connexion I2C.

* capteur de pression (carte GY63 ou GY86 basée sur MS5611, SPL06 ou BMP280) pour obtenir l'altitude et la vitesse verticale

* un capteur de pression différentielle MS4525D0_A ou SDP3X (x=1,2,3) ou SDP8xx pour obtenir la vitesse (et la vitesse verticale compensée)

* un MP6050 (acc+gyroscope ex GY86) pour améliorer le temps de réaction du vario ou pour obtenir du tangage/roulis

* 1 ou 2 ADS1115 si vous souhaitez mesurer plus de 4 tensions analogiques

## 9.1 Le GPS

Différents récepteurs GPS sont utilisables :


## 9.2 Sonde Pitot (capteur de pression différentielle)

La sonde Pitot permet de connaître la vitesse horizontale du modèle.

Il permet aussi de calculer la vitesse verticale compensée.

Différents capteurs sont utilisables :

* MS4525D0_A ou SDP3X (x=1,2,3) ou SDP8xx .

Ces capteurs sont chers, les versions SDP sont donc à privilégier.

Ces capteurs sont à câbler sur J8 avec 4 fils, 3,3v, GND, SDA et SCL.

## 9.3 Le baromètre

Le capteur BMP280 est soudé sous le RP2040.


## 9.4 Accéléromètre gyroscope

Ce capteur deux en un permet d’améliorer le temps de réaction du vario ainsi que d’obtenir les données de tangage et roulis.

On peut utiliser un MPU6050 .

Ce capteur est à câbler sur J8 avec 4 fils, 3,3v, GND, SDA et SCL.


Après câblage de ce composant, celui-ci doit être calibré.

Pour cela, il doit être placé bien à plat.

Puis on lance la commande suivante :

MPUCAL puis ENTREE

## 9.5 Les entrées analogiques du RP2040

Le RP2040 Zero possède seulement 4 entrées analogiques, V1 à V4.

Elles utilisent les pattes 26 à 29.

V1=26 V2=27 V3=28 V4=29

V1 est attribué au voltage d’un accu de propulsion et V2 au courant consommé.

V3 et V4 retournent deux tensions ou deux températures.

Pour lire des température il faudra définir :

TEMP=1 (V3 retournera une température et V4 une tensions.

TEMP=2 (V3 et V4 retourneront des températures).

Chacune des 4 entrées possèdent un pont de résistance qui doit être calculé en fonction de la tension à lire de sorte que le rp2040 reçoive un maximum de 3,3v pour la tension maximum à lire.


### 9.5.1 Tension accu moteur (V1)

Calcule du pont de résistance afin d’obtenir une tension de 3,3v pour la tension maximum.


### Pour par exemple une de 21v (4 x 4,2v soir 5S) :

R1 = 4700 Ohms (voir R1 sur le schéma)

R2 = 1000 Ohms (voir R5 sur le schéma)

Vout = 3,33v

### Par défaut, la configuration des tensions est définie ainsi :

Voltage parameters:

Scales : 1.000000 , 1.000000 , 1.000000 , 1.000000

Offsets: 0.000000 , 0.000000 , 0.000000 , 0.000000

Après câblage des bonnes résistances, on utilise un multimètre connecté entre la patte 26 du RP2040 et GND, on lit la tension sur la radio et sur le multimètre.

On va en déduire une compensation à ajouter à la configuration du RP2040.

Dans mon cas, j’ai dû définir V1 ainsi :

Voltage parameters:

Scales : 6.330000 , 50.000000 , 1.000000 , 1.000000

Offsets: 0.000000 , 82500.000000 , 0.000000 , 0.000000

### 9.5.2 Courant accu moteur (V2)


Pour lire le courant, on utilisera de préférence

un capteur de type ACFS758.

Il en existe différents types avec des courant maximum de 50A à 150A.

La tension de sortie pour les 50B, 100B et 150B est de 1,65 V.

Pas besoin donc de pont de résistance.

On utilisera donc :

R1 = 0 Ohm (voir R2 sur le schéma)

R2 = non câblé (voir R6 sur le schéma)

Donc, tout ce que vous avez à faire est de définir :

Après câblage de R2 on modifiera la configuration du RP2040 selon le modèle du ACS758.

Modèle | Scale | Offset
ACS758-50B | 25 | 41250
ACS758-100B | 50 | 82500
ACS758-150B | 75,188 | 124060,15

Dans mon cas, pour un ACS758-100B j’ai dû définir V2 ainsi :

Voltage parameters:

Scales : 6.330000 , 50.000000 , 1.000000 , 1.000000

Offsets: 0.000000 , 82500.000000 , 0.000000 , 0.000000

### 9.5.3 Tensions V3 et V4

Après câblage des bonnes résistances pour V3 (R4,R8) et V4(R3,R4), on utilise un multimètre connecté entre les pattes 28 ou 29 du RP2040 et GND, on lit la tension sur la radio et sur le multimètre.

On va en déduire une compensation à ajouter à la configuration du RP2040.

A vous de définir Scale et Offset selon vos besoins/

Voltage parameters:

Scales : 6.330000 , 50.000000 , 1.000000 , 1.000000

Offsets: 0.000000 , 82500.000000 , 0.000000 , 0.000000

### 9.5.4 Capteurs de température


En fonction du besoin, on peut utiliser un ou deux capteurs de température.

On utilisera de préférence un TMP36.

Pour un seul capteur seulement on définira :

TEMP=1

La sortie de V3 sera utilisée pour ce capteur et V4 sera utilisable pour une tension.

Pour deux capteurs, on définira :

TEMP=2

Les sorties de V3 et V4 seront alors utilisées pour deux températures.

## 9.6 Capteur compte tours


Ce capteur permet de connaître la vitesse de rotation d’un moteur.

Il utilise la patte 15 du RP2040.

On peut utiliser différents composants ou module.

- capteur Hall (ajouter une résistance entre GPIO15 et GND afin d’obtenir 3,3v maxi sur GPIO15)

- capteur IR (ajouter une résistance entre GPIO15 et GND afin d’obtenir 3,3v maxi sur GPIO15)

- module HobbyKing pour ESC

Pour le configurer, on définira :

RPM=15

En fonction du nombre de pales, on attribuera un multiplicateur.

Par exemple pour une hélice à deux pâles :

RPM_MULT=0.5

## 9.7 Les convertisseurs analogiques ADS1115

Les ADS1115, U4 et U5, sont des quadruples convertisseurs analogique/numériques.

Ils permettent de convertir 4 tensions en valeurs numériques.

L’idée d’origine était de palier à la limite de 4 entrées analogiques du RP2040 et de pouvoir

mesurer un accumulateur LIPO 8S maximum (connecteur blanc de droite).

Une autre idée serait d’utiliser ces ADS1115 comme huit entrées d’alarmes.

Il faudrait alors imaginer des alarmes dont le seuil serait définit entre 0 et 3,3v.


Pour rappel, le RP2040 ne supporte pas de tension supérieure à 3,3v en entrée !!!!

Toute tension supérieure détruira le composant !!!!

## 9.8 Sorties PWM


Si les convertisseurs analogiques ADS1115 ne sont pas utilisés, il est possible d’affecter les pattes 0 à 7 du RP2040 à 8 sorties PWM pour y connecter 8 servos.

Les résistances R18 à R34 placées entre le RP2040 et le connecteur J7 ne doivent pas être câblées.

Il faudra connecter les pattes 0 à 7 du RP2040 aux pattes 1 à 8 de J7.

Voir paragraphe 8 pour la configuration.

# 10 Réglage du Failsafe

oXs possède une fonction de Failsafe sur les sorties PWM et SBUS.

* Pour le protocole ELRS, oXs ne reçoit aucune donnée du canal RC ou des récepteurs lorsque la connexion RF est perdue. Si oXs est connecté à 2 récepteurs (via PRI et SEC), oXs générera des signaux PWM et Sbus sur les dernières données reçues. Si oXs ne reçoit plus de données du ou des récepteurs, il continuera à générer des signaux PWM et/ou SBUS en fonction de la configuration de sécurité intégrée stockée dans oXs.

* Pour les protocoles Frsky/Jeti... où Sbus, les valeurs de sécurité sont normalement définies à l'intérieur du récepteur et le récepteur continue à générer un signal Sbus même si la connexion RF est perdue. Pourtant, lorsque la connexion est perdue, le signal Sbus contient des drapeaux indiquant que certaines données sont manquantes ou que la sécurité intégrée a été appliquée. Lorsque oXs est connecté à 2 récepteurs différents, il donne la priorité au signal Sbus PRI sauf si le signal SEC est OK et PRI n'est pas OK (pas de signal, trame manquante, failsafe). Ainsi, pour Frsky/Jeti, oXs n'a pas à s'occuper de sa propre configuration de sécurité (sauf si oXs ne recoit plus de signal Sbus - par exemple en raison d'un problème de câblage).

* Le failsafe oXs a 3 options :

* "Hold" = failsafe sera les dernières valeurs des canaux Rc connus juste avant que la connexion ne soit perdue ; pour sélectionner cette option, utilisez l'interface série avec la commande FAILSAFE=H.

* Sauvegarder comme sécurité intégrée les valeurs actuelles des canaux RC à l'aide de l'interface série avec la commande SETFAILSAFE.

* Sauvegarder en tant que sécurité intégrée les valeurs actuelles des canaux RC à l'aide du bouton "boot" du RP2040. Pour activer cette option, double-cliquez sur le bouton. La led doit devenir bleue fixe. Dans les 5 secondes suivantes, appuyez et maintenez le bouton "boot". La led deviendra blanche pendant 2 secondes confirmant que les valeurs sont enregistrées.

Pour les 2 dernières options, l’émetteur doit être allumé et générer les valeurs des canaux que vous souhaitez enregistrer dans oXs.

11 Documentations

Une documentation (https://github.com/mstrens/oXs_on_RP2040/blob/test/doc/fields%20per%20protocol.txt) très précise pour chaque protocole est disponible sur le github de Michel Strens.

On peut y trouver les différentes valeurs des ID par porotocole.

Page 20 Manuel utilisateur oXs RP2040 v1.0

Page 5 Manuel utilisateur oXs RP2040 v1.0

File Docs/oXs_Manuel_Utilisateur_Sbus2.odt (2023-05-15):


oXs RP2040

Nouvelle version

openXsensor

pour un RP2040-Zero

Manuel Utilisateur Futaba Sbus2

# 1 Alimentation

## 1.1 Alimentation du module

Le circuit imprimé est équipé d’un régulateur de tension 5v.

Il peut être mis en ou hors fonction selon l’accu de réception utilisé.

Accus inférieur ou égal à 5V :


Accus supérieur à 5V :


## 1.2 Limite du RP2040

Le RP2040 ne supporte pas de tension supérieure à 3,3v en entrée !!!!

Toute tension supérieure détruira le composant !!!!

# 2 Futaba Sbus2


PROTOCOL=2 PRI=9 SEC=255 TLM=8

3 Les capteurs

3.1 Le GPS

Différents récepteurs GPS sont utilisables :


## 3.2 Le baromètre

Le capteur BMP280 est déjà soudé sous le RP2040.


## 3.3 Sonde Pitot (capteur de pression différentielle)


La sonde Pitot permet de connaître la vitesse horizontale du modèle.

Il permet aussi de calculer la vitesse verticale compensée.

Différents capteurs sont utilisables :

* MS4525D0_A ou SDP3X (x=1,2,3) ou SDP8xx .

Ces capteurs sont chers, les versions SDP sont donc à privilégier.

Ces capteurs sont à câbler sur J8 avec 4 fils, 3,3v, GND, SDA et SCL.

## 3.4 Accéléromètre gyroscope

Ce capteur deux en un permet d’améliorer le temps de réaction du vario ainsi que d’obtenir les données de tangage et roulis.

On peut utiliser un MPU6050 .

Ce capteur est à câbler sur J8 avec 4 fils, 3,3v, GND, SDA et SCL.


Après câblage de ce composant, celui-ci doit être calibré.

Pour cela, il doit être placé bien à plat.

Puis on lance la commande suivante :

MPUCAL puis ENTREE

## 3.5 Les entrées analogiques du RP2040

Le RP2040 Zero possède seulement 4 entrées analogiques, V1 à V4.

Elles utilisent les pattes 26 à 29.

V1=26 V2=27 V3=28 V4=29

V1 est attribué au voltage d’un accu de propulsion et V2 au courant consommé.

V3 et V4 retournent deux tensions ou deux températures.

Pour lire des température il faudra définir :

TEMP=1 (V3 retournera une température et V4 une tensions.

TEMP=2 (V3 et V4 retourneront des températures).

Chacune des 4 entrées possèdent un pont de résistance qui doit être calculé en fonction de la tension à lire de sorte que le rp2040 reçoive un maximum de 3,3v pour la tension maximum à lire.


### 3.5.1 Tension et courant accu moteur (V1/V2)


Pour lire le courant, on utilisera de préférence

un capteur de type ACFS758.

Il en existe différents types avec des courant maximum de 50A à 150A.

La tension de sortie pour les 50B, 100B et 150B est de 1,65 V.

Pas besoin donc de pont de résistance.

### 3.5.2 Tensions V3 et V4

Après câblage des bonnes résistances pour V3 (R4,R8) et V4(R3,R4), il est possible de lire deux tensions supplémentaires.

### 3.5.3 Capteurs de température V3 et V4


En fonction du besoin, on peut utiliser un ou deux capteurs de température.

On utilisera de préférence un TMP36.

Pour un seul capteur seulement on définira :

TEMP=1

La sortie de V3 sera utilisée pour ce capteur et V4 sera utilisable pour une tension.

Pour deux capteurs, on définira :

TEMP=2

Les sorties de V3 et V4 seront alors utilisées pour deux températures.

## 3.6 Capteur compte tours


Ce capteur permet de connaître la vitesse de rotation d’un moteur.

Il utilise la patte 15 du RP2040.

On peut utiliser différents composants ou module.

- capteur Hall

- capteur IR

- module HobbyKing pour ESC

Pour le configurer, on définira :

RPM=15

En fonction du nombre de pales, on attribuera un multiplicateur.

Par exemple pour une hélice à deux pâles :

RPM_MULT=0.5

## 3.7 Les convertisseurs analogiques ADS1115

Les ADS1115, U4 et U5, sont des quadruples convertisseurs analogique/numériques.

Ils permettent de convertir 4 tensions en valeurs numériques.

L’idée d’origine était de palier à la limite de 4 entrées analogiques du RP2040 et de pouvoir

mesurer un accumulateur LIPO 8S maximum (connecteur blanc de droite).

Une autre idée serait d’utiliser ces ADS1115 comme huit entrées d’alarmes.

Il faudrait alors imaginer des alarmes dont le seuil serait définit entre 0 et 3,3v.


Pour rappel, le RP2040 ne supporte pas de tension supérieure à 3,3v en entrée !!!!

Toute tension supérieure détruira le composant !!!!

## 3.8 Sorties PWM


Si les convertisseurs analogiques ADS1115 ne sont pas utilisés, il est possible d’affecter les pattes 0 à 7 du RP2040 à 8 sorties PWM pour y connecter 8 servos.

Les résistances R18 à R34 placées entre le RP2040 et le connecteur J7 ne doivent pas être câblées.

Il faudra connecter les pattes 0 à 7 du RP2040 aux pattes 1 à 8 de J7.

Voir paragraphe 8 pour la configuration.

# 4 Configuration radio

## 4.1 Recherche des capteurs

- Brancher le module oXs un l’entrée de télémétrie Sbus2 du récepteur Futaba.

- Allumer le récepteur.

- Créer un nouveau modèle avec le protocole Futaba.

- Réaliser l’appairage du récepteur à l’émetteur (BIND).

- Aller dans l’écran de télémétrie du modèle et lancer une recherche des capteurs.

En fonction des capteurs connectés au module oXs, plusieurs lignes devraient apparaître en plus de la tension accu réception, Rssi etc.

Le GPS ne recevra pas bien s’il est utilisé en intérieur. Il met minimum 1mn pour commencer à recevoir.

Après la découverte d’au moins 4 satellites, les cordonnées ainsi que la date et l’heure, l’altitude, la vitesse horizontale et plus devraient apparaître.

Le baromètre doit retourner l’altitude par rapport au sol ainsi que la vitesse verticale.

Que l’on soit au niveau de la mer ou à 1000m d’altitude, il donnera zéro au démarrage.

C’est donc une altitude relative, pas absolue.

- Stopper la recherche des capteurs.

- Configurer Vario avec Alt .

## 4.1 Utilisation des valeurs de télémétrie dans les écrans

Les radios Futaba disposent de pages d’écrans définissables avec ce que l’on souhaite visualiser facilement et rapidement.

On pourra facilement visualiser toutes les valeurs de télémétrie dans ces écrans.

Il est aussi possible de définir des alarmes en fonctions des valeurs de télémétrie reçues.

Page 0 Manuel utilisateur oXs RP2040 v1.0

Page 8 Manuel utilisateur oXs RP2040 v1.0

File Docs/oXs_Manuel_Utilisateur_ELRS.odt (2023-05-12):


oXs RP2040

Nouvelle version

openXsensor

pour un RP2040-Zero

Manuel Utilisateur ExpressLRS

# 1 Alimentation

## 1.1 Alimentation du module

Le circuit imprimé est équipé d’un régulateur de tension 5v.

Il peut être mis en ou hors fonction selon l’accu de réception utilisé.

Accus inférieur ou égal à 5V : (utiliser le connecteur de dessous)


Accus supérieur à 5V : (utiliser le connecteur de dessous)


## 1.2 Limite du RP2040

Le RP2040 ne supporte pas de tension supérieure à 3,3v en entrée !!!!

Toute tension supérieure détruira le composant !!!!

# 2 ExpressLRS (CRSF)


PROTOCOL C PRI=9 TLM=8 SBUS_OUT=0

ELRS permet de commander des servos via la sortie SbuS ou via les sorties PWM C1 à C16.

C1=1 C2=2 C3=3 C4=4 etc.

3 Les capteurs

3.1 Le GPS

Différents récepteurs GPS sont utilisables :


## 3.2 Le baromètre

Le capteur BMP280 est déjà soudé sous le RP2040.


## 3.3 Sonde Pitot (capteur de pression différentielle)


La sonde Pitot permet de connaître la vitesse horizontale du modèle.

Il permet aussi de calculer la vitesse verticale compensée.

Différents capteurs sont utilisables :

* MS4525D0_A ou SDP3X (x=1,2,3) ou SDP8xx .

Ces capteurs sont chers, les versions SDP sont donc à privilégier.

Ces capteurs sont à câbler sur J8 avec 4 fils, 3,3v, GND, SDA et SCL.

## 3.4 Accéléromètre gyroscope

Ce capteur deux en un permet d’améliorer le temps de réaction du vario ainsi que d’obtenir les données de tangage et roulis.

On peut utiliser un MPU6050 .

Ce capteur est à câbler sur J8 avec 4 fils, 3,3v, GND, SDA et SCL.


Après câblage de ce composant, celui-ci doit être calibré.

Pour cela, il doit être placé bien à plat.

Puis on lance la commande suivante :

MPUCAL puis ENTREE

## 3.5 Les entrées analogiques du RP2040

Le RP2040 Zero possède seulement 4 entrées analogiques, V1 à V4.

Elles utilisent les pattes 26 à 29.

V1=26 V2=27 V3=28 V4=29

V1 est attribué au voltage d’un accu de propulsion et V2 au courant consommé.

V3 et V4 retournent deux tensions ou deux températures.

Pour lire des température il faudra définir :

TEMP=1 (V3 retournera une température et V4 une tensions.

TEMP=2 (V3 et V4 retourneront des températures).

Chacune des 4 entrées possèdent un pont de résistance qui doit être calculé en fonction de la tension à lire de sorte que le rp2040 reçoive un maximum de 3,3v pour la tension maximum à lire.


### 3.5.1 Tension et courant accu moteur (V1/V2)


Pour lire le courant, on utilisera de préférence

un capteur de type ACFS758.

Il en existe différents types avec des courant maximum de 50A à 150A.

La tension de sortie pour les 50B, 100B et 150B est de 1,65 V.

Pas besoin donc de pont de résistance.

### 3.5.2 Tensions V3 et V4

Après câblage des bonnes résistances pour V3 (R4,R8) et V4(R3,R4), il est possible de lire deux tensions supplémentaires.

### 3.5.3 Capteurs de température V3 et V4


En fonction du besoin, on peut utiliser un ou deux capteurs de température.

On utilisera de préférence un TMP36.

Pour un seul capteur seulement on définira :

TEMP=1

La sortie de V3 sera utilisée pour ce capteur et V4 sera utilisable pour une tension.

Pour deux capteurs, on définira :

TEMP=2

Les sorties de V3 et V4 seront alors utilisées pour deux températures.

## 3.6 Capteur compte tours


Ce capteur permet de connaître la vitesse de rotation d’un moteur.

Il utilise la patte 15 du RP2040.

On peut utiliser différents composants ou module.

- capteur Hall

- capteur IR

- module HobbyKing pour ESC

Pour le configurer, on définira :

RPM=15

En fonction du nombre de pales, on attribuera un multiplicateur.

Par exemple pour une hélice à deux pâles :

RPM_MULT=0.5

## 3.7 Les convertisseurs analogiques ADS1115

Les ADS1115, U4 et U5, sont des quadruples convertisseurs analogique/numériques.

Ils permettent de convertir 4 tensions en valeurs numériques.

L’idée d’origine était de palier à la limite de 4 entrées analogiques du RP2040 et de pouvoir

mesurer un accumulateur LIPO 8S maximum (connecteur blanc de droite).

Une autre idée serait d’utiliser ces ADS1115 comme huit entrées d’alarmes.

Il faudrait alors imaginer des alarmes dont le seuil serait définit entre 0 et 3,3v.


Pour rappel, le RP2040 ne supporte pas de tension supérieure à 3,3v en entrée !!!!

Toute tension supérieure détruira le composant !!!!

## 3.8 Sorties PWM


Si les convertisseurs analogiques ADS1115 ne sont pas utilisés, il est possible d’affecter les pattes 0 à 7 du RP2040 à 8 sorties PWM pour y connecter 8 servos.

Les résistances R18 à R34 placées entre le RP2040 et le connecteur J7 ne doivent pas être câblées.

Il faudra connecter les pattes 0 à 7 du RP2040 aux pattes 1 à 8 de J7.

Voir paragraphe 8 pour la configuration.

# 4 Configuration radio

## 4.1 Recherche des capteurs

- Brancher le module oXs au récepteur ExpressLRS.

- Allumer le récepteur.

- Créer un nouveau modèle avec le protocole CRSF.

- Réaliser l’appairage du récepteur à l’émetteur (BIND),sauf si l’appairage est déjà réalisé grâce à mot de passe via le programme de configuration ExpressLRS Configurator (https://github.com/ExpressLRS/ExpressLRS-Configurator/releases).

- Aller dans l’écran de télémétrie du modèle et lancer une recherche des capteurs.

En fonction des capteurs connectés au module oXs, plusieurs lignes devraient apparaître en plus de la tension accu réception, Rssi etc.

Le GPS ne recevra pas bien s’il est utilisé en intérieur. Il met minimum 1mn pour commencer à recevoir.

Après la découverte d’au moins 4 satellites, les cordonnées ainsi que la date et l’heure, l’altitude, la vitesse horizontale et plus devraient apparaître.

Le baromètre doit retourner l’altitude par rapport au sol ainsi que la vitesse verticale.

Que l’on soit au niveau de la mer ou à 1000m d’altitude, il donnera zéro au démarrage.

C’est donc une altitude relative, pas absolue.

- Stopper la recherche des capteurs.

- Configurer Vario avec Alt .

## 4.1 Utilisation des valeurs de télémétrie dans les écrans

Les radios supportant les modules ExpressLRS disposent de pages d’écrans définissables avec ce que l’on souhaite visualiser facilement et rapidement.

On pourra facilement visualiser toutes les valeurs de télémétrie dans ces écrans.

Il est aussi possible de définir des alarmes en fonctions des valeurs de télémétrie reçues.

Page 0 Manuel utilisateur oXs RP2040 v1.0

Page 8 Manuel utilisateur oXs RP2040 v1.0

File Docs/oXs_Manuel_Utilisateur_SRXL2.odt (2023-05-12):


oXs RP2040

Nouvelle version

openXsensor

pour un RP2040-Zero

Manuel Utilisateur Spektrum

# 1 Alimentation

## 1.1 Alimentation du module

Le circuit imprimé est équipé d’un régulateur de tension 5v.

Il peut être mis en ou hors fonction selon l’accu de réception utilisé.

Accus inférieur ou égal à 5V : (utiliser le connecteur de dessous)


Accus supérieur à 5V : (utiliser le connecteur de dessous)


## 1.2 Limite du RP2040

Le RP2040 ne supporte pas de tension supérieure à 3,3v en entrée !!!!

Toute tension supérieure détruira le composant !!!!

# 2 Spektrum (SRXL2)

Il existe plusieurs types de récepteur Spektrum, avec ou sans sorties servo.


PROTOCOL L PRI=9 TLM=255 SBUS_OUT=0

SRXL2 permet de commander des servos via la sortie SbuS ou via les sorties PWM C1 à C16.

C1=1 C2=2 C3=3 C4=4 etc.

3 Les capteurs

3.1 Le GPS

Différents récepteurs GPS sont utilisables :


## 3.2 Le baromètre

Le capteur BMP280 est déjà soudé sous le RP2040.


## 3.3 Sonde Pitot (capteur de pression différentielle)


La sonde Pitot permet de connaître la vitesse horizontale du modèle.

Il permet aussi de calculer la vitesse verticale compensée.

Différents capteurs sont utilisables :

* MS4525D0_A ou SDP3X (x=1,2,3) ou SDP8xx .

Ces capteurs sont chers, les versions SDP sont donc à privilégier.

Ces capteurs sont à câbler sur J8 avec 4 fils, 3,3v, GND, SDA et SCL.

## 3.4 Accéléromètre gyroscope

Ce capteur deux en un permet d’améliorer le temps de réaction du vario ainsi que d’obtenir les données de tangage et roulis.

On peut utiliser un MPU6050 .

Ce capteur est à câbler sur J8 avec 4 fils, 3,3v, GND, SDA et SCL.


Après câblage de ce composant, celui-ci doit être calibré.

Pour cela, il doit être placé bien à plat.

Puis on lance la commande suivante :

MPUCAL puis ENTREE

## 3.5 Les entrées analogiques du RP2040

Le RP2040 Zero possède seulement 4 entrées analogiques, V1 à V4.

Elles utilisent les pattes 26 à 29.

V1=26 V2=27 V3=28 V4=29

V1 est attribué au voltage d’un accu de propulsion et V2 au courant consommé.

V3 et V4 retournent deux tensions ou deux températures.

Pour lire des température il faudra définir :

TEMP=1 (V3 retournera une température et V4 une tensions.

TEMP=2 (V3 et V4 retourneront des températures).

Chacune des 4 entrées possèdent un pont de résistance qui doit être calculé en fonction de la tension à lire de sorte que le rp2040 reçoive un maximum de 3,3v pour la tension maximum à lire.


### 3.5.1 Tension et courant accu moteur (V1/V2)


Pour lire le courant, on utilisera de préférence

un capteur de type ACFS758.

Il en existe différents types avec des courant maximum de 50A à 150A.

La tension de sortie pour les 50B, 100B et 150B est de 1,65 V.

Pas besoin donc de pont de résistance.

### 3.5.2 Tensions V3 et V4

Après câblage des bonnes résistances pour V3 (R4,R8) et V4(R3,R4), il est possible de lire deux tensions supplémentaires.

### 3.5.3 Capteurs de température V3 et V4


En fonction du besoin, on peut utiliser un ou deux capteurs de température.

On utilisera de préférence un TMP36.

Pour un seul capteur seulement on définira :

TEMP=1

La sortie de V3 sera utilisée pour ce capteur et V4 sera utilisable pour une tension.

Pour deux capteurs, on définira :

TEMP=2

Les sorties de V3 et V4 seront alors utilisées pour deux températures.

## 3.6 Capteur compte tours


Ce capteur permet de connaître la vitesse de rotation d’un moteur.

Il utilise la patte 15 du RP2040.

On peut utiliser différents composants ou module.

- capteur Hall

- capteur IR

- module HobbyKing pour ESC

Pour le configurer, on définira :

RPM=15

En fonction du nombre de pales, on attribuera un multiplicateur.

Par exemple pour une hélice à deux pâles :

RPM_MULT=0.5

## 3.7 Les convertisseurs analogiques ADS1115

Les ADS1115, U4 et U5, sont des quadruples convertisseurs analogique/numériques.

Ils permettent de convertir 4 tensions en valeurs numériques.

L’idée d’origine était de palier à la limite de 4 entrées analogiques du RP2040 et de pouvoir

mesurer un accumulateur LIPO 8S maximum (connecteur blanc de droite).

Une autre idée serait d’utiliser ces ADS1115 comme huit entrées d’alarmes.

Il faudrait alors imaginer des alarmes dont le seuil serait définit entre 0 et 3,3v.


Pour rappel, le RP2040 ne supporte pas de tension supérieure à 3,3v en entrée !!!!

Toute tension supérieure détruira le composant !!!!

## 3.8 Sorties PWM


Si les convertisseurs analogiques ADS1115 ne sont pas utilisés, il est possible d’affecter les pattes 0 à 7 du RP2040 à 8 sorties PWM pour y connecter 8 servos.

Les résistances R18 à R34 placées entre le RP2040 et le connecteur J7 ne doivent pas être câblées.

Il faudra connecter les pattes 0 à 7 du RP2040 aux pattes 1 à 8 de J7.

Voir paragraphe 8 pour la configuration.

# 4 Configuration radio

## 4.1 Recherche des capteurs

- Brancher le module oXs au récepteur ExpressLRS.

- Allumer le récepteur.

- Créer un nouveau modèle avec le protocole CRSF.

- Réaliser l’appairage du récepteur à l’émetteur (BIND),sauf si l’appairage est déjà réalisé grâce à mot de passe via le programme de configuration ExpressLRS Configurator (https://github.com/ExpressLRS/ExpressLRS-Configurator/releases).

- Aller dans l’écran de télémétrie du modèle et lancer une recherche des capteurs.

En fonction des capteurs connectés au module oXs, plusieurs lignes devraient apparaître en plus de la tension accu réception, Rssi etc.

Le GPS ne recevra pas bien s’il est utilisé en intérieur. Il met minimum 1mn pour commencer à recevoir.

Après la découverte d’au moins 4 satellites, les cordonnées ainsi que la date et l’heure, l’altitude, la vitesse horizontale et plus devraient apparaître.

Le baromètre doit retourner l’altitude par rapport au sol ainsi que la vitesse verticale.

Que l’on soit au niveau de la mer ou à 1000m d’altitude, il donnera zéro au démarrage.

C’est donc une altitude relative, pas absolue.

- Stopper la recherche des capteurs.

- Configurer Vario avec Alt .

## 4.1 Utilisation des valeurs de télémétrie dans les écrans

Les radios supportant les modules ExpressLRS disposent de pages d’écrans définissables avec ce que l’on souhaite visualiser facilement et rapidement.

On pourra facilement visualiser toutes les valeurs de télémétrie dans ces écrans.

Il est aussi possible de définir des alarmes en fonctions des valeurs de télémétrie reçues.

Page 0 Manuel utilisateur oXs RP2040 v1.0

Page 5 Manuel utilisateur oXs RP2040 v1.0

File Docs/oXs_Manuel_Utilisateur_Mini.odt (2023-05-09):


oXs RP2040

Nouvelle version

openXsensor

pour un RP2040-Zero

Manuel Utilisateur oXs RP2040

# 1 Alimentation

## 1.1 Alimentation du module

Le circuit imprimé est équipé d’un régulateur de tension 5v.

Il peut être mis en ou hors fonction selon l’accu de réception utilisé.

Accus inférieur ou égal à 5V :


Accus supérieur à 5V :


## 1. Limite du RP2040

Le RP2040 ne supporte pas de tension supérieure à 3,3v en entrée !!!!

Toute tension supérieure détruira le composant !!!!

# 2 Les protocoles

## 2.1 S-Port, Hott, M-Link, Ibus, Jeti Ex


S-Port PROTOCOL=S

Hott PROTOCOL=H

M-link PROTOCOL=M

Ibus PROTOCOL=I

Jeti Ex PROTOCOL=J

PRI=255 SEC=255 TLM=8

## 2.2 Sbus2, Srxl2, Jeti ExBus, Fbus


Sbus2 PROTOCOL=2

Fbus PROTOCOL=F

Srxl2 PROTOCOL=L

Jeti Exbus PROTOCOL=E

PRI=9 SEC=255 TLM=255

## 2.3 ExpressLRS


ExpressLRS PROTOCOL=C

PRI=9 SEC=255 TLM=8

# 3 Utilisation de deux récepteurs

# 4 Les capteurs

Les capteurs utilisent différentes connexions au RP2040.

- Le GPS utilise une liaison série.

- Les 4 tensions V1 à V4 utilisent une 4 entrées analogiques.

- Le tachymètre utilise une entrée numérique.

- Tous les autres capteurs utilisent une connexion I2C.

* capteur de pression (carte GY63 ou GY86 basée sur MS5611, SPL06 ou BMP280) pour obtenir l'altitude et la vitesse verticale

* un capteur de pression différentielle MS4525D0_A ou SDP3X (x=1,2,3) ou SDP8xx pour obtenir la vitesse (et la vitesse verticale compensée)

* un MP6050 (acc+gyroscope ex GY86) pour améliorer le temps de réaction du vario ou pour obtenir du tangage/roulis

* 1 ou 2 ADS1115 si vous souhaitez mesurer plus de 4 tensions analogiques

## 4.1 Le GPS

Différents récepteurs GPS sont utilisables :


## 4.2 Sonde Pitot (capteur de pression différentielle)

La sonde Pitot permet de connaître la vitesse horizontale du modèle.

Il permet aussi de calculer la vitesse verticale compensée.

Différents capteurs sont utilisables :

* MS4525D0_A ou SDP3X (x=1,2,3) ou SDP8xx .

Ces capteurs sont chers, les versions SDP sont donc à privilégier.

Ces capteurs sont à câbler sur J8 avec 4 fils, 3,3v, GND, SDA et SCL.


## 4.3 Le baromètre

Le capteur BMP280 est soudé sous le RP2040.


## 4.4 Accéléromètre gyroscope

Ce capteur deux en un permet d’améliorer le temps de réaction du vario ainsi que d’obtenir les données de tangage et roulis.

On peut utiliser un MPU6050 .

Ce capteur est à câbler sur J8 avec 4 fils, 3,3v, GND, SDA et SCL.


Après câblage de ce composant, celui-ci doit être calibré.

Pour cela, il doit être placé bien à plat.

Puis on lance la commande suivante :

MPUCAL puis ENTREE

## 4.5 Les entrées analogiques du RP2040

Le RP2040 Zero possède seulement 4 entrées analogiques, V1 à V4.

Elles utilisent les pattes 26 à 29.

V1=26 V2=27 V3=28 V4=29

V1 est attribué au voltage d’un accu de propulsion et V2 au courant consommé.

V3 et V4 retournent deux tensions ou deux températures.

Pour lire des température il faudra définir :

TEMP=1 (V3 retournera une température et V4 une tensions.

TEMP=2 (V3 et V4 retourneront des températures).

Chacune des 4 entrées possèdent un pont de résistance qui doit être calculé en fonction de la tension à lire de sorte que le rp2040 reçoive un maximum de 3,3v pour la tension maximum à lire.


### 4.5.1 Tension accu moteur (V1)

Calcule du pont de résistance afin d’obtenir une tension de 3,3v pour la tension maximum.


### Pour par exemple une de 21v (4 x 4,2v soir 5S) :

R1 = 4700 Ohms (voir R1 sur le schéma)

R2 = 1000 Ohms (voir R5 sur le schéma)

Vout = 3,33v

### Par défaut, la configuration des tensions est définie ainsi :

Voltage parameters:

Scales : 1.000000 , 1.000000 , 1.000000 , 1.000000

Offsets: 0.000000 , 0.000000 , 0.000000 , 0.000000

Après câblage des bonnes résistances, on utilise un multimètre connecté entre la patte 26 du RP2040 et GND, on lit la tension sur la radio et sur le multimètre.

On va en déduire une compensation à ajouter à la configuration du RP2040.

Dans mon cas, j’ai dû définir V1 ainsi :

Voltage parameters:

Scales : 6.330000 , 50.000000 , 1.000000 , 1.000000

Offsets: 0.000000 , 82500.000000 , 0.000000 , 0.000000

### 4.5.2 Courant accu moteur (V2)


Pour lire le courant, on utilisera de préférence

un capteur de type ACFS758.

Il en existe différents types avec des courant maximum de 50A à 150A.

La tension de sortie pour les 50B, 100B et 150B est de 1,65 V.

Pas besoin donc de pont de résistance.

On utilisera donc :

R1 = 0 Ohm (voir R2 sur le schéma)

R2 = non câblé (voir R6 sur le schéma)

Donc, tout ce que vous avez à faire est de définir :

Après câblage de R2 on modifiera la configuration du RP2040 selon le modèle du ACS758.

Modèle | Scale | Offset
ACS758-50B | 25 | 41250
ACS758-100B | 50 | 82500
ACS758-150B | 75,188 | 124060,15

Dans mon cas, pour un ACS758-100B j’ai dû définir V2 ainsi :

Voltage parameters:

Scales : 6.330000 , 50.000000 , 1.000000 , 1.000000

Offsets: 0.000000 , 82500.000000 , 0.000000 , 0.000000

### 4.5.3 Tensions V3 et V4

Après câblage des bonnes résistances pour V3 (R4,R8) et V4(R3,R4), on utilise un multimètre connecté entre les pattes 28 ou 29 du RP2040 et GND, on lit la tension sur la radio et sur le multimètre.

On va en déduire une compensation à ajouter à la configuration du RP2040.

A vous de définir Scale et Offset selon vos besoins/

Voltage parameters:

Scales : 6.330000 , 50.000000 , 1.000000 , 1.000000

Offsets: 0.000000 , 82500.000000 , 0.000000 , 0.000000

### 4.5.4 Capteurs de température


En fonction du besoin, on peut utiliser un ou deux capteurs de température.

On utilisera de préférence un TMP36.

Pour un seul capteur seulement on définira :

TEMP=1

La sortie de V3 sera utilisée pour ce capteur et V4 sera utilisable pour une tension.

Pour deux capteurs, on définira :

TEMP=2

Les sorties de V3 et V4 seront alors utilisées pour deux températures.

## 4.6 Capteur compte tours


Ce capteur permet de connaître la vitesse de rotation d’un moteur.

Il utilise la patte 15 du RP2040.

On peut utiliser différents composants ou module.

- capteur Hall

- capteur IR

- module HobbyKing pour ESC

Pour le configurer, on définira :

RPM=15

En fonction du nombre de pales, on attribuera un multiplicateur.

Par exemple pour une hélice à deux pâles :

RPM_MULT=0.5

## 4.7 Les convertisseurs analogiques ADS1115

Les ADS1115, U4 et U5, sont des quadruples convertisseurs analogique/numériques.

Ils permettent de convertir 4 tensions en valeurs numériques.

L’idée d’origine était de palier à la limite de 4 entrées analogiques du RP2040 et de pouvoir

mesurer un accumulateur LIPO 8S maximum (connecteur blanc de droite).

Une autre idée serait d’utiliser ces ADS1115 comme huit entrées d’alarmes.

Il faudrait alors imaginer des alarmes dont le seuil serait définit entre 0 et 3,3v.


Pour rappel, le RP2040 ne supporte pas de tension supérieure à 3,3v en entrée !!!!

Toute tension supérieure détruira le composant !!!!

## 4.8 Sorties PWM


Si les convertisseurs analogiques ADS1115 ne sont pas utilisés, il est possible d’affecter les pattes 0 à 7 du RP2040 à 8 sorties PWM pour y connecter 8 servos.

Les résistances R18 à R34 placées entre le RP2040 et le connecteur J7 ne doivent pas être câblées.

Il faudra connecter les pattes 0 à 7 du RP2040 aux pattes 1 à 8 de J7.

Voir paragraphe 8 pour la configuration.

# 5 Réglage du Failsafe

oXs possède une fonction de Failsafe sur les sorties PWM et SBUS.

* Pour le protocole ELRS, oXs ne reçoit aucune donnée du canal RC ou des récepteurs lorsque la connexion RF est perdue. Si oXs est connecté à 2 récepteurs (via PRI et SEC), oXs générera des signaux PWM et Sbus sur les dernières données reçues. Si oXs ne reçoit plus de données du ou des récepteurs, il continuera à générer des signaux PWM et/ou SBUS en fonction de la configuration de sécurité intégrée stockée dans oXs.

* Pour les protocoles Frsky/Jeti... où Sbus, les valeurs de sécurité sont normalement définies à l'intérieur du récepteur et le récepteur continue à générer un signal Sbus même si la connexion RF est perdue. Pourtant, lorsque la connexion est perdue, le signal Sbus contient des drapeaux indiquant que certaines données sont manquantes ou que la sécurité intégrée a été appliquée. Lorsque oXs est connecté à 2 récepteurs différents, il donne la priorité au signal Sbus PRI sauf si le signal SEC est OK et PRI n'est pas OK (pas de signal, trame manquante, failsafe). Ainsi, pour Frsky/Jeti, oXs n'a pas à s'occuper de sa propre configuration de sécurité (sauf si oXs ne recoit plus de signal Sbus - par exemple en raison d'un problème de câblage).

* Le failsafe oXs a 3 options :

* "Hold" = failsafe sera les dernières valeurs des canaux Rc connus juste avant que la connexion ne soit perdue ; pour sélectionner cette option, utilisez l'interface série avec la commande FAILSAFE=H.

* Sauvegarder comme sécurité intégrée les valeurs actuelles des canaux RC à l'aide de l'interface série avec la commande SETFAILSAFE.

* Sauvegarder en tant que sécurité intégrée les valeurs actuelles des canaux RC à l'aide du bouton "boot" du RP2040. Pour activer cette option, double-cliquez sur le bouton. La led doit devenir bleue fixe. Dans les 5 secondes suivantes, appuyez et maintenez le bouton "boot". La led deviendra blanche pendant 2 secondes confirmant que les valeurs sont enregistrées.

Pour les 2 dernières options, l’émetteur doit être allumé et générer les valeurs des canaux que vous souhaitez enregistrer dans oXs.

11 Documentations

Une documentation (https://github.com/mstrens/oXs_on_RP2040/blob/test/doc/fields%20per%20protocol.txt) très précise pour chaque protocole est disponible sur le github de Michel Strens.

On peut y trouver les différentes valeurs des ID par porotocole.

Page 15 Manuel utilisateur oXs RP2040 v1.0

Page 4 Manuel utilisateur oXs RP2040 v1.0

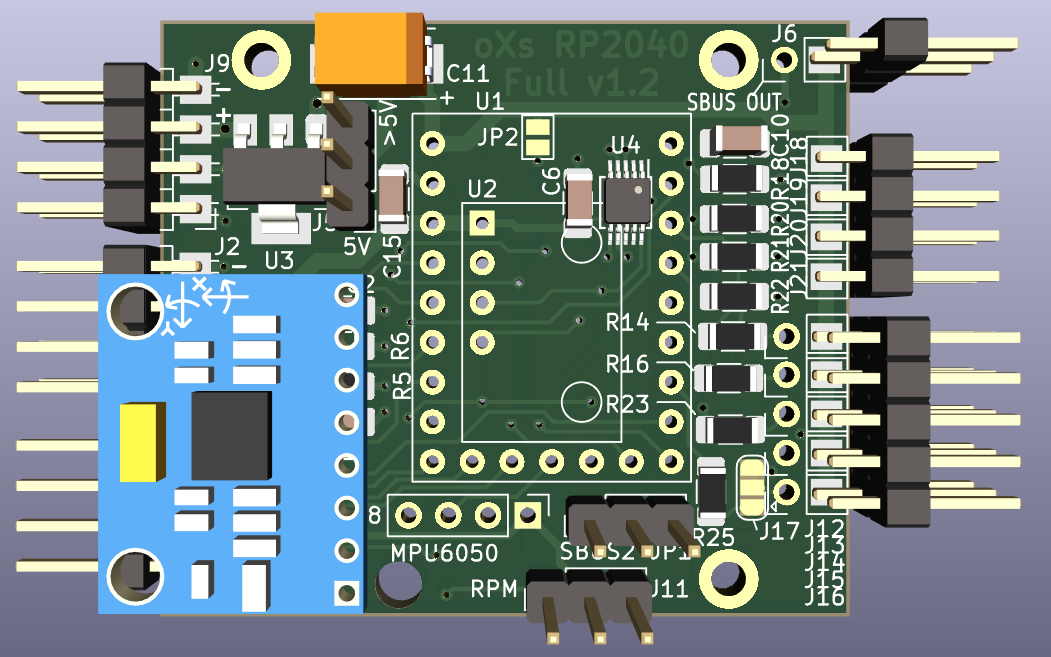
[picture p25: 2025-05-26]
V1.2/Top_WithMPU.png

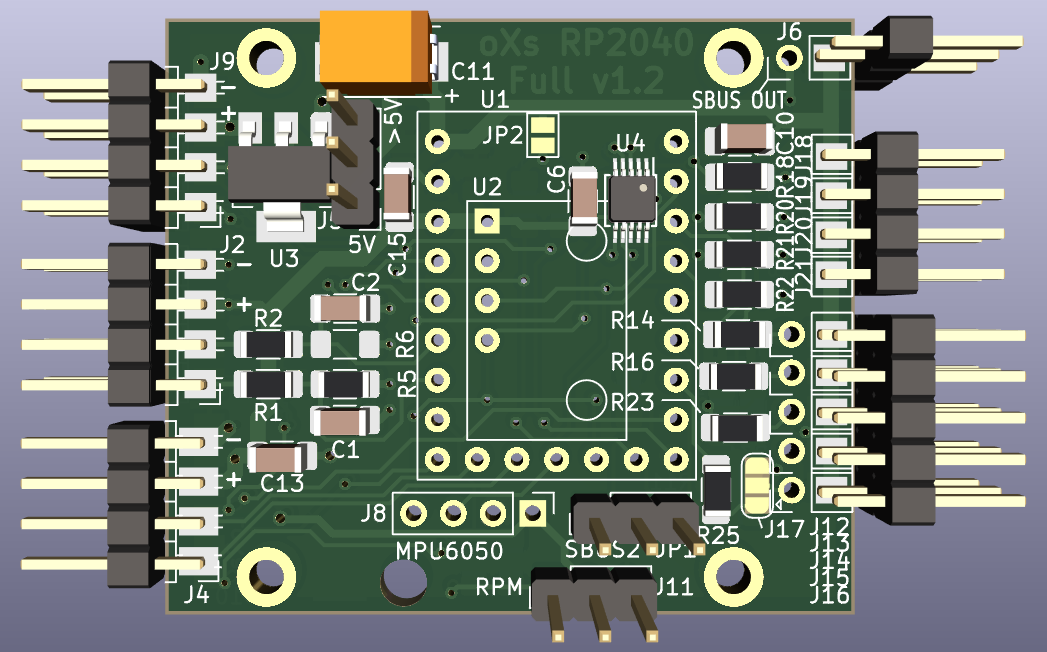
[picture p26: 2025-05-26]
V1.2/Top_NoBPM280-NoMPU.png

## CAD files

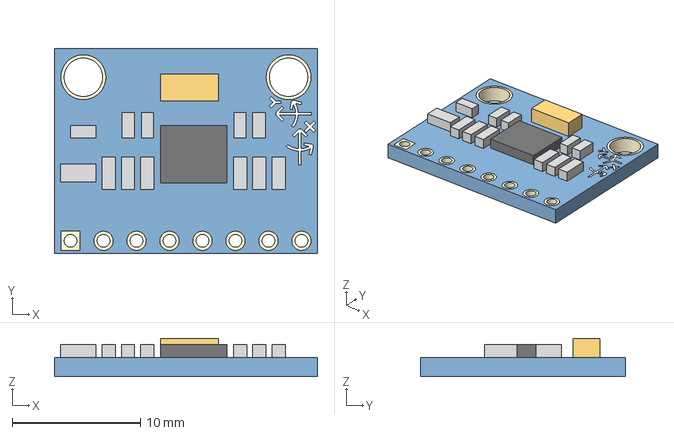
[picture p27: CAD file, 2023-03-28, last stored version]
oXs_RP2040_Full/MPU_6050.step
20.5 x 16.0 x 3.00 mm

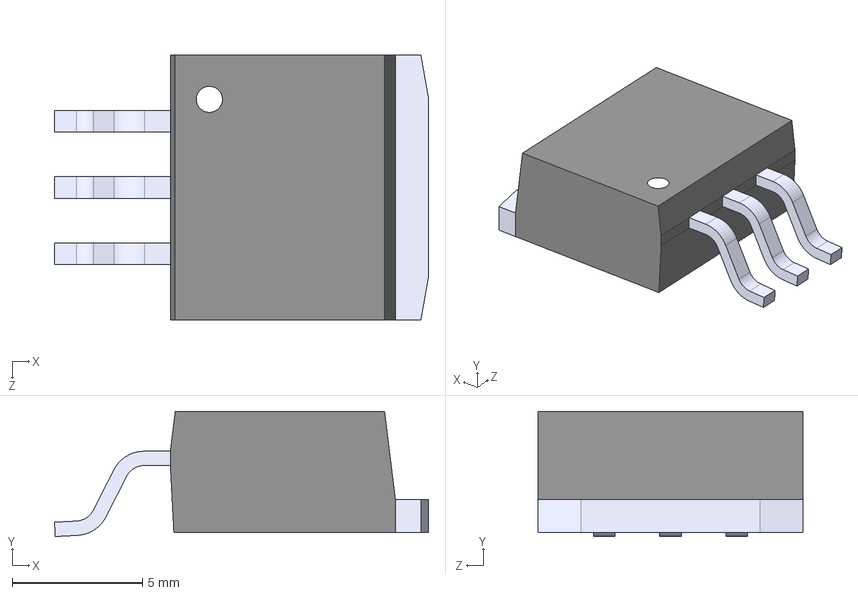
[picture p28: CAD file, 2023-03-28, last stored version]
oXs_RP2040_Full/LM2940SX-10_NOPB.step
14.4 x 4.80 x 10.2 mm

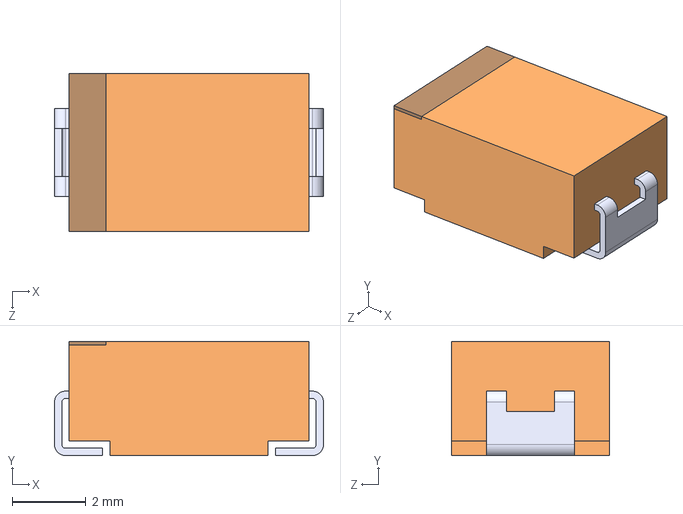
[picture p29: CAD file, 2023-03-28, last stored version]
oXs_RP2040_Full/TCJD226M035R0100.step
7.30 x 3.10 x 4.30 mm

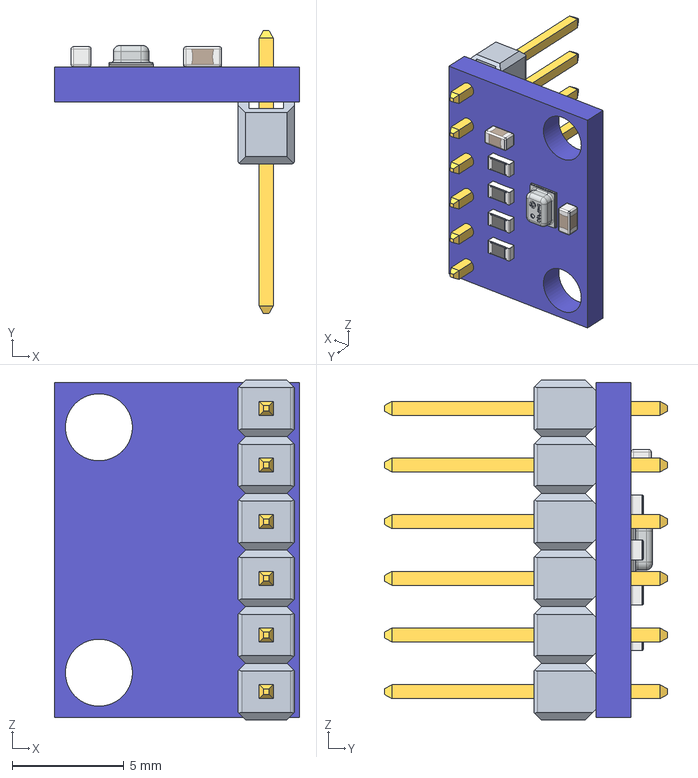
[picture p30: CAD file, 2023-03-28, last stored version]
oXs_RP2040_Full/bmp280_module.stp
11.0 x 12.7 x 15.2 mm

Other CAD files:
oXs_RP2040_Full/MPU_6050.stl

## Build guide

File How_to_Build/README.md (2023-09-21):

# How to wire oXs board

<table border="2">
<tr>
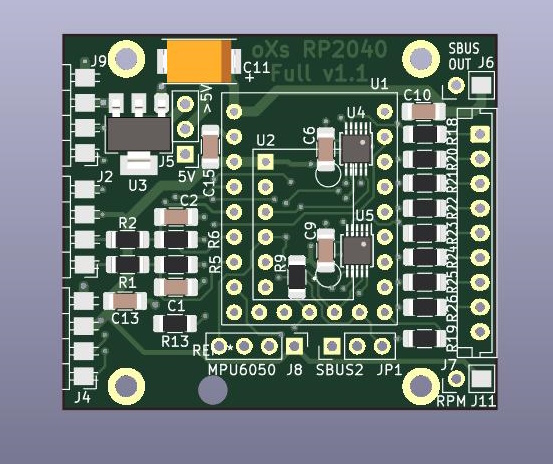
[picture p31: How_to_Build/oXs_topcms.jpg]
<td></td>
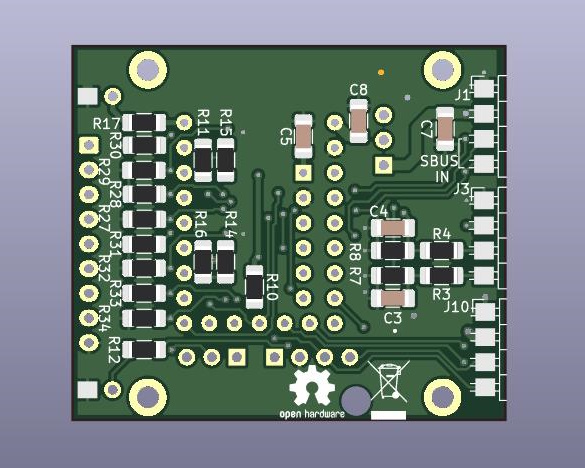
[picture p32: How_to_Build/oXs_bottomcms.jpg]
<td></td>
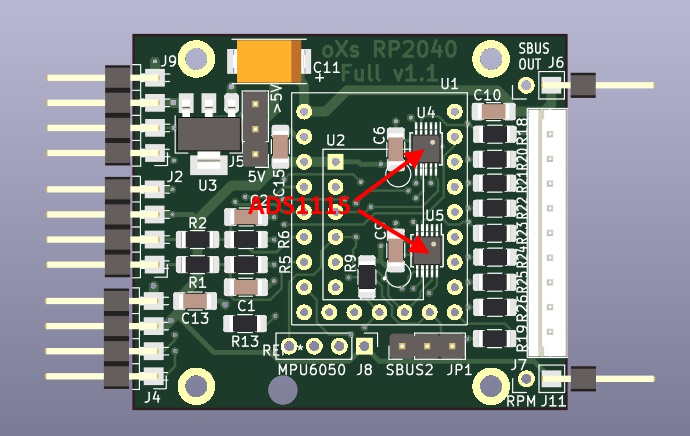
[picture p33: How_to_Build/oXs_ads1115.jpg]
<td></td>
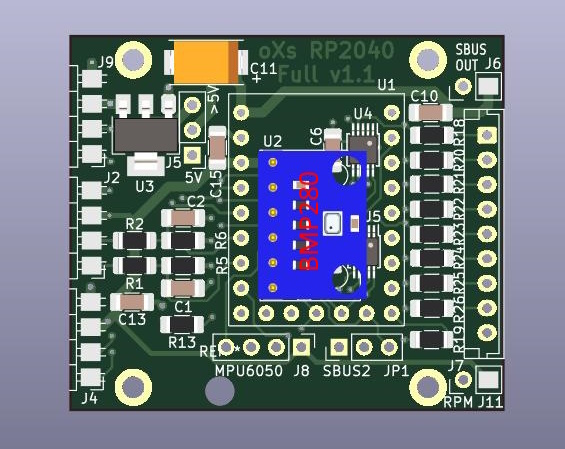
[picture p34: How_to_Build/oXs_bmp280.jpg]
<td></td>
</tr>
<tr>
<td>     #1</td><td>     #2</td><td>     #3</td><td>     #4</td>
</tr>
<tr>
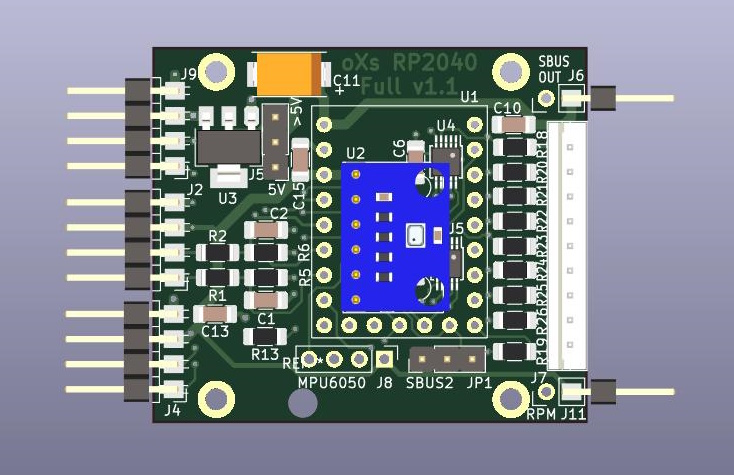
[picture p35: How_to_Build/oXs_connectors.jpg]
<td></td>
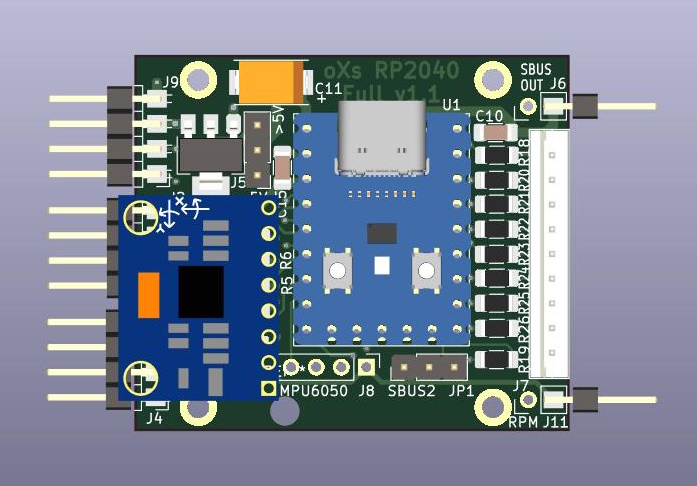
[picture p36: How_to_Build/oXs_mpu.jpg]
<td></td>
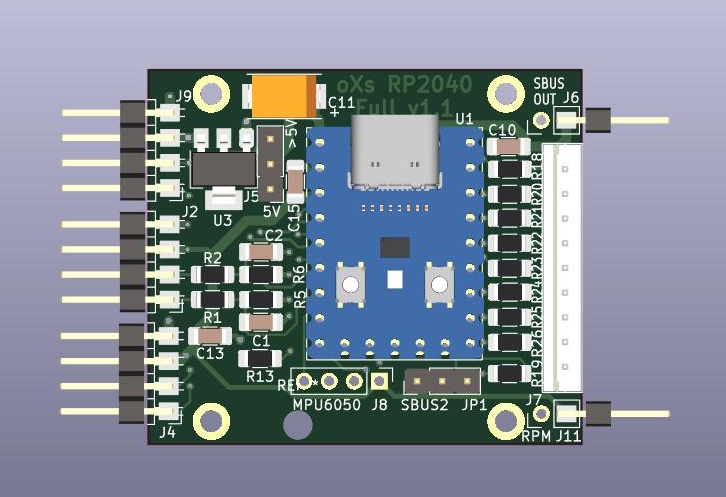
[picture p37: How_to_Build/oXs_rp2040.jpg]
<td></td>
</tr>
<tr>
<td>     #5</td><td>     #6</td><td>     #7</td>
</tr>
</table>

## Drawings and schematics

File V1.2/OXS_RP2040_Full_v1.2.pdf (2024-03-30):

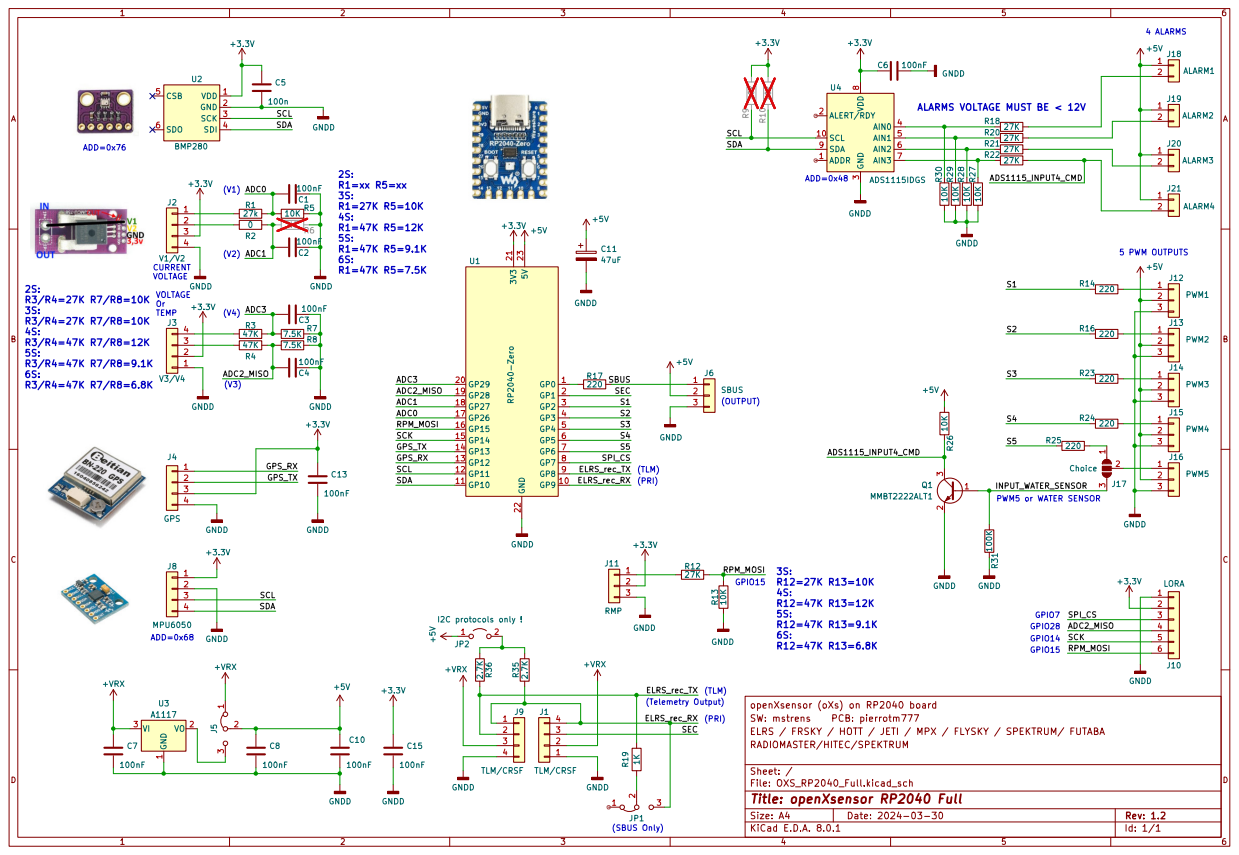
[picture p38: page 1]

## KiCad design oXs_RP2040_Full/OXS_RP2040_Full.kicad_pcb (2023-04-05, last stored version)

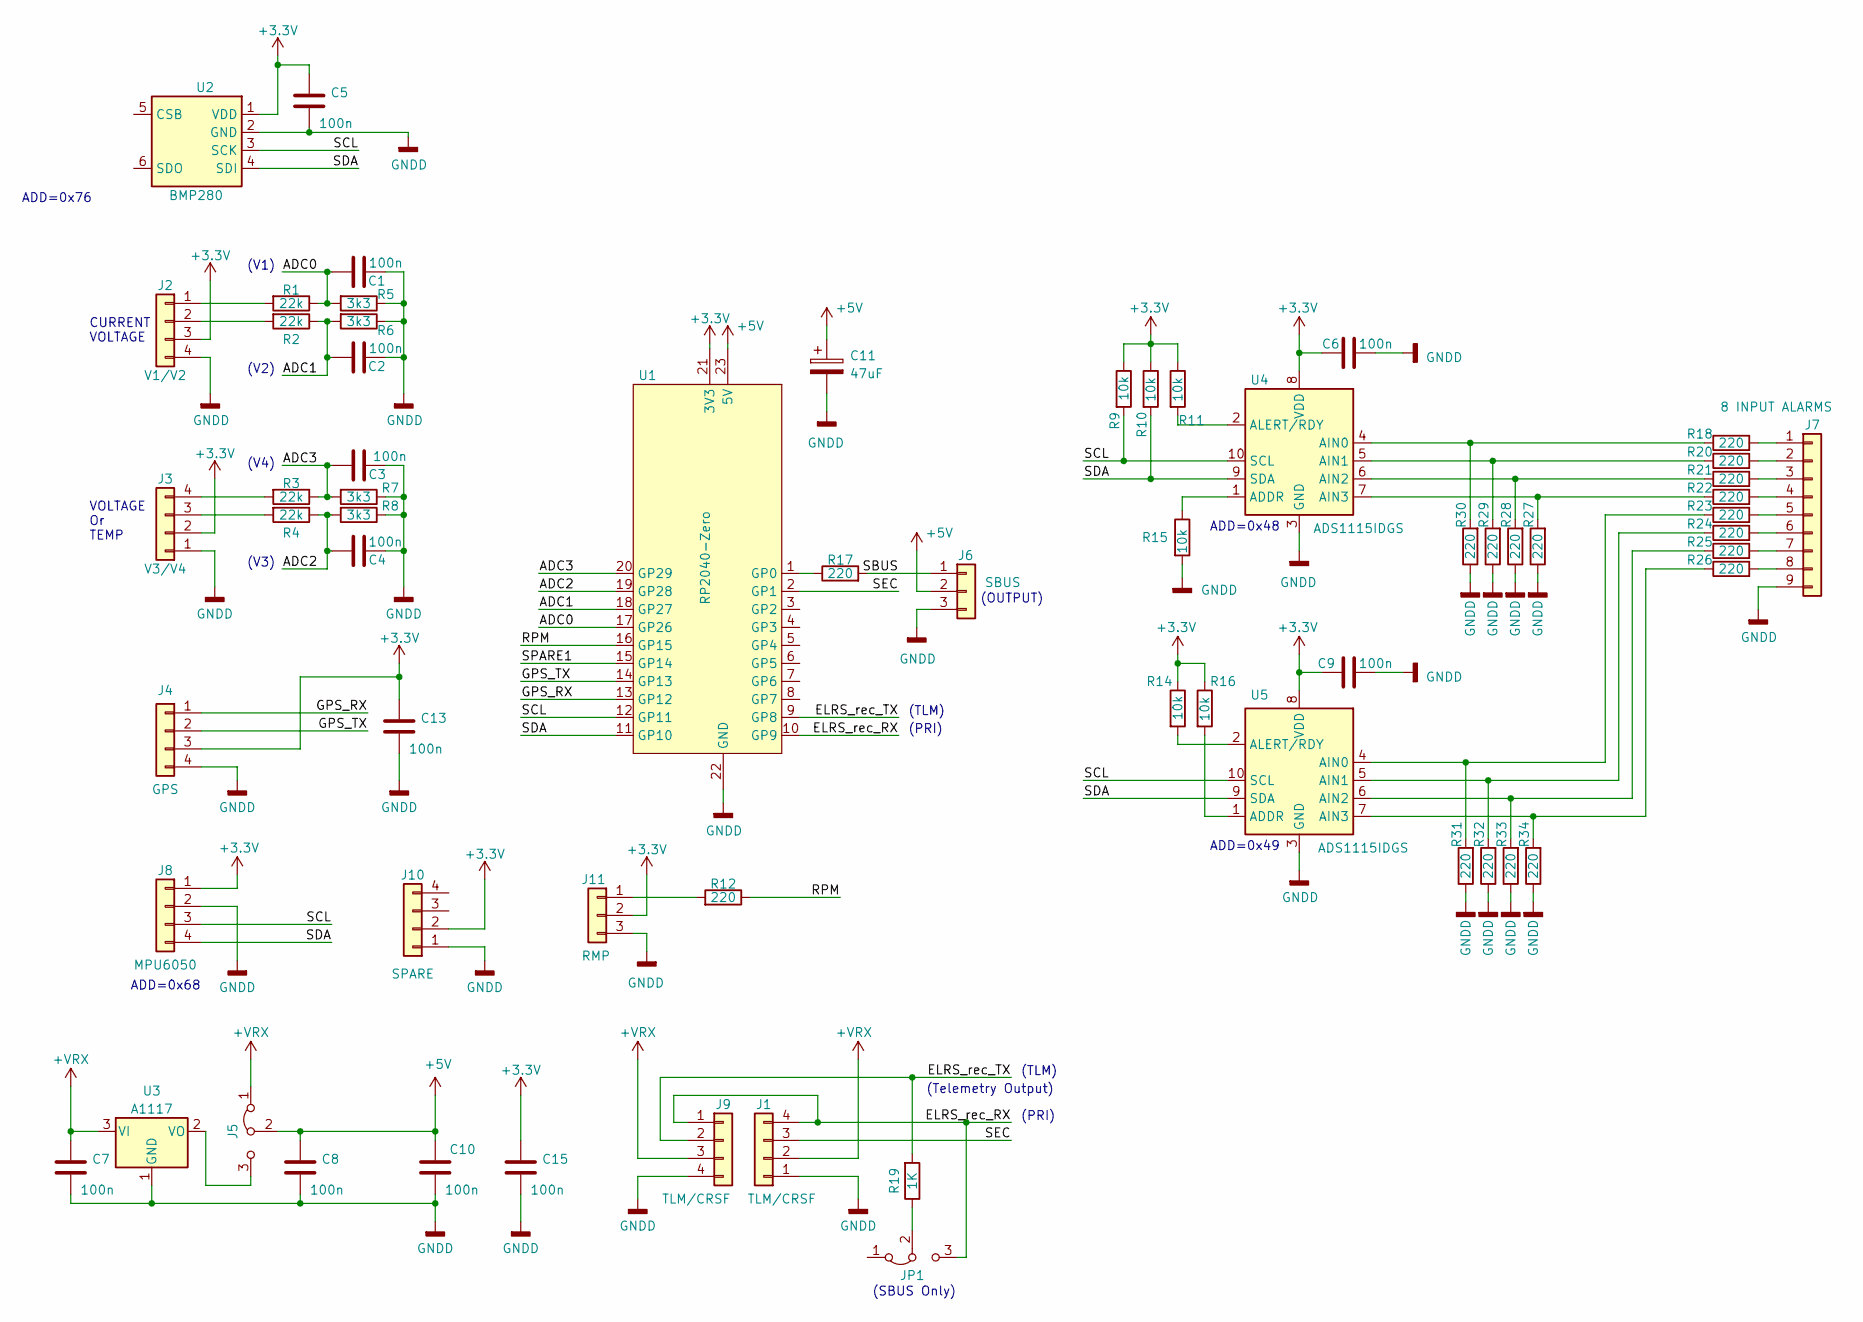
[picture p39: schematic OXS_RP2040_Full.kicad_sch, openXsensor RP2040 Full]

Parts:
C1, C2, C3, C4, C5, C6, C7, C8, C9, C10, C13, C15: 100n; C_1206_3216Metric_Pad1.33x1.80mm_HandSolder
C11: 47uF; CAPPM7343X310N
J1, J9: TLM/CRSF; PinHeader_1x04_P2.54mm_Horizontal_Mod
J2: V1/V2; PinHeader_1x04_P2.54mm_Horizontal_Mod
J3: V3/V4; PinHeader_1x04_P2.54mm_Horizontal_Mod
J4: GPS; PinHeader_1x04_P2.54mm_Horizontal_Mod
J5: SELECT_POWER; PinHeader_1x03_P2.54mm_Vertical
J6: SBUS; Pin_Header_Straight_1x03_Mod_Pitch2.54mm
J7: 8 INPUT ALARMS; JST_EH_B9B-EH-A_1x09_P2.50mm_Vertical
J8: MPU6050; PinHeader_1x04_P2.54mm_Vertical
J10: SPARE; PinHeader_1x04_P2.54mm_Horizontal_Mod
J11: RMP; Pin_Header_Straight_1x03_Mod_Pitch2.54mm
JP1: SBUS2; PinHeader_1x03_P2.54mm_Vertical
R1, R2, R3, R4: 22k; R_1206_3216Metric_Pad1.30x1.75mm_HandSolder
R5, R6, R7, R8: 3k3; R_1206_3216Metric_Pad1.30x1.75mm_HandSolder
R9, R10, R11, R14, R15, R16: 10k; R_1206_3216Metric_Pad1.30x1.75mm_HandSolder
R12, R17, R18, R20, R21, R22, R23, R24, R25, R26, R27, R28, R29, R30, R31, R32, R33, R34: 220; R_1206_3216Metric_Pad1.30x1.75mm_HandSolder
R19: 1K; R_1206_3216Metric_Pad1.30x1.75mm_HandSolder
U1: RP2040-Zero
U2: BMP280
U3: A1117; SOT-223-3_TabPin2
U4, U5: ADS1115IDGS; TSSOP-10_3x3mm_P0.5mm

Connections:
+3.3V: C5.1, C6.2, C9.2, C13.1, C15.1, J2.3, J3.2, J4.3, J8.1, J10.2, J11.2, R9.1, R10.1, R11.1, R14.1, R16.1, U1.21 (3V3), U2.1 (VDD), U4.8 (VDD), U5.8 (VDD)
+5V: C8.1, C10.1, C11.1, J5.2 (C), J6.2, U1.23 (5V)
+VRX: C7.1, J1.2, J5.1 (A), J9.3, U3.3 (VI)
/ADC0: C1.2, R1.1, R5.2, U1.17 (GP26)
/ADC1: C2.2, R2.1, R6.2, U1.18 (GP27)
/ADC2: C4.2, R4.1, R8.2, U1.19 (GP28)
/ADC3: C3.2, R3.1, R7.2, U1.20 (GP29)
/ELRS_rec_RX: J1.4, J9.1, JP1.3 (B), U1.10 (GP9)
/ELRS_rec_TX: J9.2, R19.2, U1.9 (GP8)
/GPS_RX: J4.1, U1.13 (GP12)
/GPS_TX: J4.2, U1.14 (GP13)
/RPM: R12.1, U1.16 (GP15)
/SBUS: J6.1, R17.2
/SCL: J8.3, R9.2, U1.12 (GP11), U2.3 (SCK), U4.10 (SCL), U5.10 (SCL)
/SDA: J8.4, R10.2, U1.11 (GP10), U2.4 (SDI), U4.9 (SDA), U5.9 (SDA)
/SEC: J1.3, U1.2 (GP1)
/SPARE1: U1.15 (GP14)
GNDD: C1.1, C2.1, C3.1, C4.1, C5.2, C6.1, C7.2, C8.2, C9.1, C10.2, C11.2, C13.2, C15.2, J1.1, J2.4, J3.1, J4.4, J6.3, J7.9, J8.2, J9.4, J10.1, J11.3, R5.1, R6.1, R7.1, R8.1, R15.2, R27.1, R28.1, R29.1, R30.1, R31.1, R32.1, R33.1, R34.1, U1.22 (GND), U2.2 (GND), U3.1 (GND), U4.3 (GND), U5.3 (GND)
unnamed: J2.1, R1.2
unnamed: J2.2, R2.2
unnamed: J3.3, R4.2
unnamed: J3.4, R3.2
unnamed: J5.3 (B), U3.2 (VO)
unnamed: J7.1, R18.2
unnamed: J7.2, R20.2
unnamed: J7.3, R21.2
unnamed: J7.4, R22.2
unnamed: J7.5, R23.2
unnamed: J7.6, R24.2
unnamed: J7.7, R25.2
unnamed: J7.8, R26.2
unnamed: J11.1, R12.2
unnamed: JP1.2 (C), R19.1
unnamed: R17.1, U1.1 (GP0)
unnamed: R15.1, U4.1 (ADDR)
unnamed: R18.1, R30.2, U4.4 (AIN0)
unnamed: R20.1, R29.2, U4.5 (AIN1)
unnamed: R21.1, R28.2, U4.6 (AIN2)
unnamed: R22.1, R27.2, U4.7 (AIN3)
unnamed: R11.2, U4.2 (ALERT/RDY)
unnamed: R16.2, U5.1 (ADDR)
unnamed: R23.1, R31.2, U5.4 (AIN0)
unnamed: R24.1, R32.2, U5.5 (AIN1)
unnamed: R25.1, R33.2, U5.6 (AIN2)
unnamed: R26.1, R34.2, U5.7 (AIN3)
unnamed: R14.2, U5.2 (ALERT/RDY)

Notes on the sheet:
CURRENT VOLTAGE
(SBUS Only)
(V4)
ADD=0x49
(TLM)
(PRI)
(V2)
VOLTAGE Or TEMP
(OUTPUT)
(V1)
ADD=0x48
(Telemetry Output)
ADD=0x76
(V3)
ADD=0x68

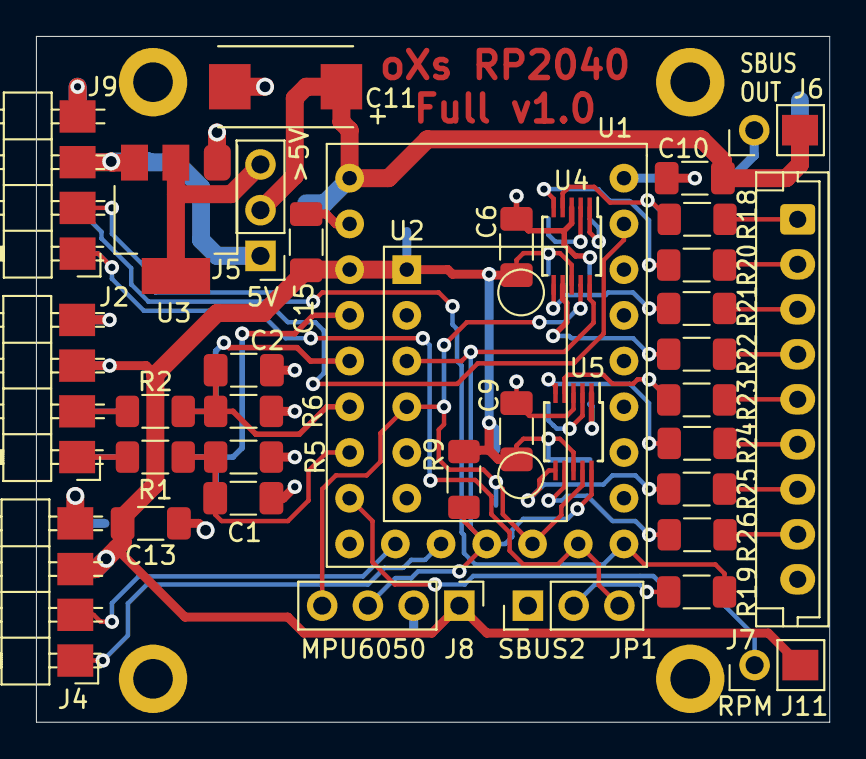
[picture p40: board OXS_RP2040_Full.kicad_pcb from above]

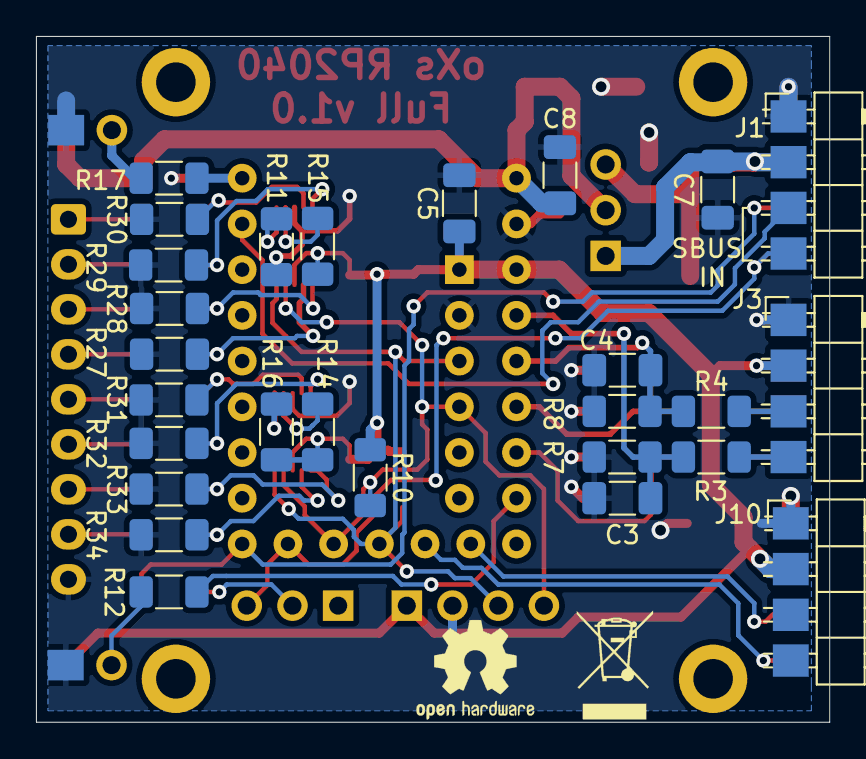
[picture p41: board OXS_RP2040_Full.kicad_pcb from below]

Board: 2 copper layers, 44.1 x 38.1 mm, 63 parts (27 on the bottom side), 45 nets.

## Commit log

2023-03-28 Add Kicad files & Gerber
    [LM2940SX-10_NOPB.step, MPU_6050.step, MPU_6050.stl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]
2023-04-02 replace mpu6050 connection
    [OXS_RP2040_Full-B_Adhesive.gbr, OXS_RP2040_Full-B_Cu.gbr, OXS_RP2040_Full-B_Fab.gbr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]
2023-04-02 little adds
    [OXS_RP2040_Full-B_Adhesive.gbr, OXS_RP2040_Full-B_Cu.gbr, OXS_RP2040_Full-B_Fab.gbr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]
2023-04-05 update / build gerber
    [OXS_RP2040_Full-B_Adhesive.gbr, OXS_RP2040_Full-B_Cu.gbr, OXS_RP2040_Full-B_Fab.gbr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]
2023-04-30 Add Voltages, current and Rpm sensors
2023-05-01 Update current sensor
2023-05-05 Add PWM outputs
2023-09-07 Update to v1.1
    [LM2940SX-10_NOPB.step, MPU_6050.step, MPU_6050.stl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]
2023-09-21 Add how to build oxs board
2024-03-30 Update v1.2
    move connectors for a 2.54mm space
2025-05-26 rename kicad files
